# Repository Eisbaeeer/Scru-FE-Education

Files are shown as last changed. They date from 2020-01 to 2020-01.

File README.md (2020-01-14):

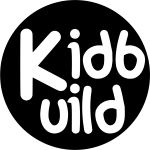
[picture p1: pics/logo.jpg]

# Scru-FE-Education
ESP8266 controlled Scru-FE with routed parts   
Inspirations from : https://www.thingiverse.com/thing:780050

## Beschreibung
Dieses Projekt soll Jugendlichen ab 12 Jahren die Programmierung von Microcontrollern näher bringen. Das Projekt ist dafür 
ausgelegt, z.B. Aktionen als Ferienprogramm anzubieten. Die zeitliche Planung sollte zwei Tage beinhalten. Am ersten Tag wird 
der Roboter aus den gefrästen Teilen zusammengebaut, am zweiten Tag wird er dann programmiert. Weitere Informationen zu dem 
Projekt findet man unter http://www.kidbuild.de
 
## Verzeichnisstruktur
- pics = Bilder
- source = Arduino Sketch
- docs = Anleitung für die Montage des Roboters
- dxf = Fräsdaten für CNC Bearbeitung (4mm Pappel Sperrholz)

## Projektbilder
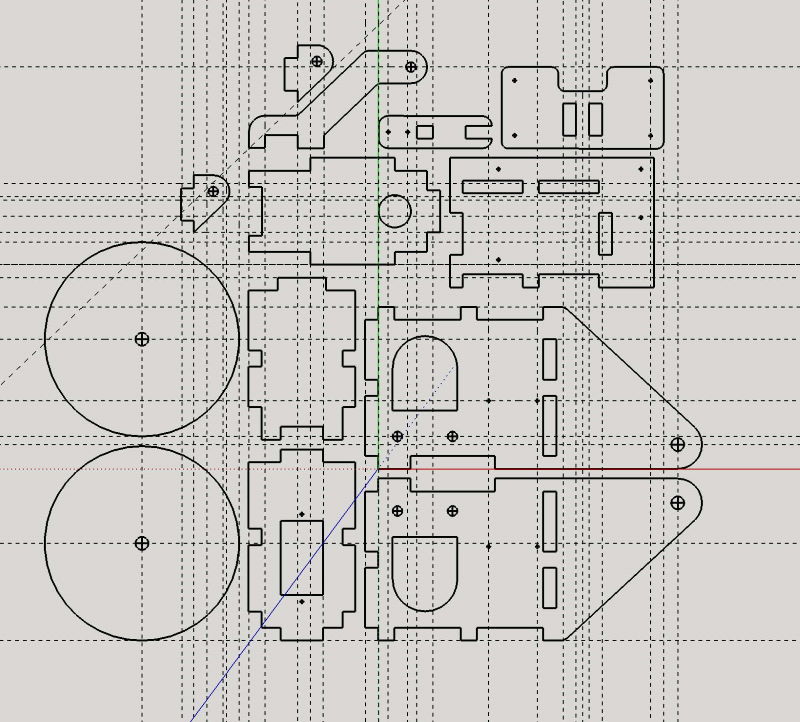
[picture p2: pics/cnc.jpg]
   
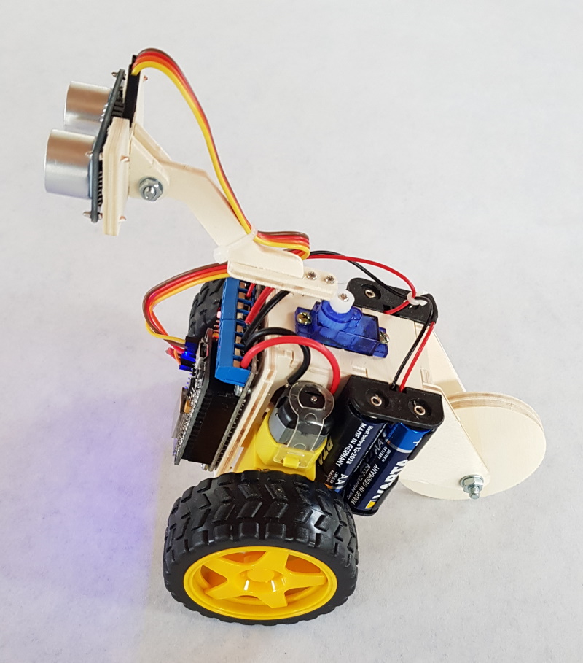
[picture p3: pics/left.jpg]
   
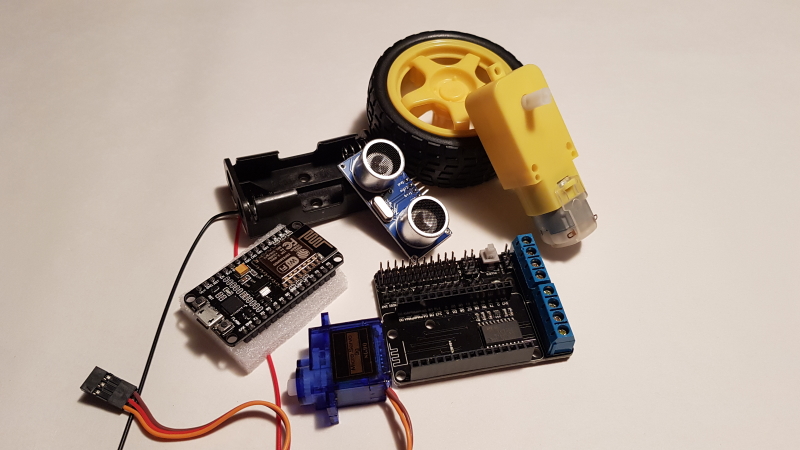
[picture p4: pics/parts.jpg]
   
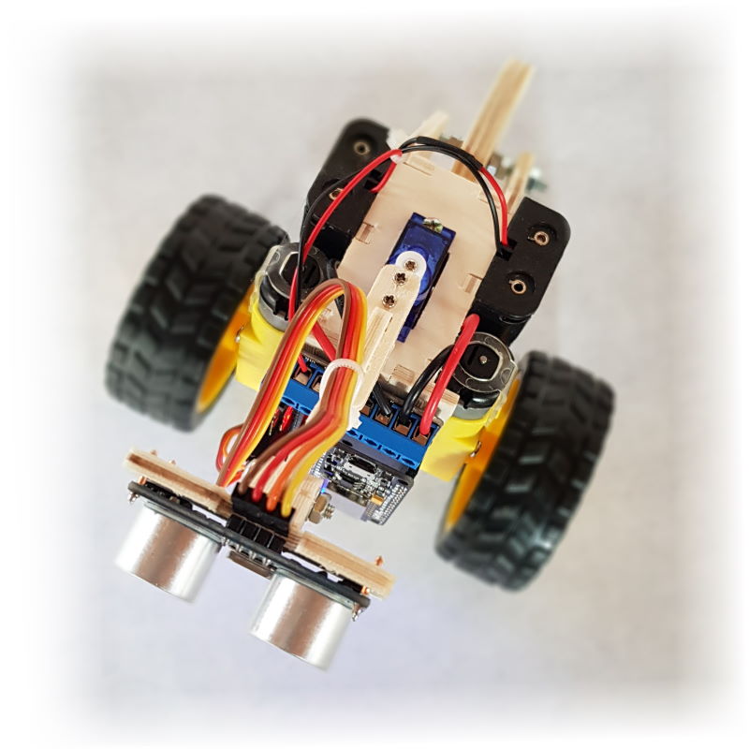
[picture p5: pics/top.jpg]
   

## Changelog

### 1.0
- (Eisbaeeer)
Initial Version

## License
The MIT License (MIT)
Copyright (c) 2019 Eisbaeeer <eisbaeeer@gmail.com>

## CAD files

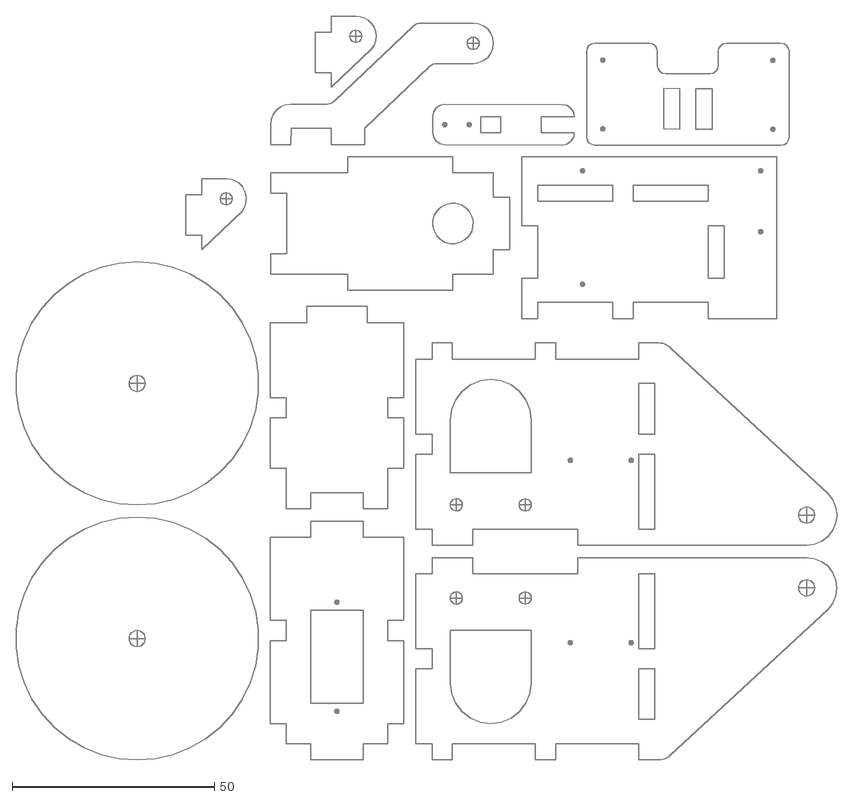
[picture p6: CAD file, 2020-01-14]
dxf/Korpus.dxf
202.8 x 183.7

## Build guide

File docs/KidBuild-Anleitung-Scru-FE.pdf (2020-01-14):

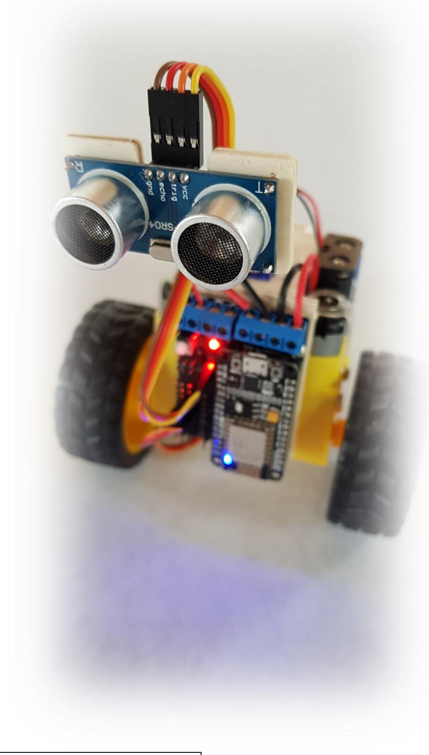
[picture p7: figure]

S e i t e 1 | 26

## SKRU-FE AUFBAU ANLEITUNG

Version | Datum | Bemerkung
1.0 | 13.04.2019 | Initial

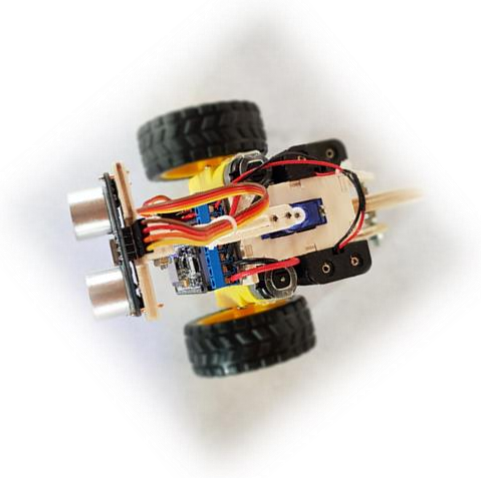
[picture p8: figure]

Roboter lern Projekt www.kidbuild.de

S e i t e 2 | 26

EINLEITUNG

Diese Anleitung hilft Dir dabei, Deinen Scru-FE mit der bebilderten Anleitung Stück für Stück zusammen zu bauen.

Die Teile sind CNC gefräst und müssen noch mit einem Taschenmesser oder scharfer Klinge ausgelöst werden.

Du kannst die Holzteile noch mit Acryl Farbe lackieren oder auch einfach so verwenden.

Der Scru-FE ist nur die Basis für Deine eigenen Ideen. Er lässt sich um weitere Funktionen ergänzen.

Zur Basis gehören die Funktionen ferngesteuertes fahren und autonomes fahren.

Du benötigst dazu lediglich ein WLAN fähiges Gerät mit Browser. Das kann ein Handy oder Tablet sein.

Für das autonome fahren benötigst du kein weiteres Gerät, Dein Scru-FE reicht aus.

Für die Programmierung verwendest du das kostenlose Programm Arduino-IDE. Die Software ist Open-Source und für Windows, Mac und Linux verfügbar.

Dein Scru-FE hat noch freie Schnittstellen, mit denen du Deine eigene Ideen wie Scheinwerfer, Blinklicht, Kamera und viele andere Dinge realisieren kannst.

Weitere Ideen und Anleitungen findest du unter

www.kidbuild.de

Jetzt kann es losgehen! Viel Spaß mit Deinem

SCRU-FE

S e i t e 3 | 26

BAUTEILE
Als erstes löst ihr die gefrästen Teile heraus. Dazu mit einem Taschenmesser oder einer Klinge die Stege vorsichtig von beiden Seiten trennen.

Tipp: Mit einem Schleifpapier die Teile nacharbeiten.

VERLEIMEN DER TEILE

## - Teil G (Frontplatte)

## - Teil I (Seitenteil rechts)

Als erste Teile benötigt ihr die Front (Teil G) und das rechte Seitenteil (Teil I).

Schaut Euch die Zeichnung rechts nochmals genau an und prüft, ob ihr die richtigen Teile vor Euch liegen habt.

Gebt nun auf den Rand zwischen den beiden Teilen ein wenig Holzleim oder Bastelkleber und steckt sie zusammen.

Achtet dabei auf die Frontplatte. Die flache Kante muss nach unten zeigen. Das zweite Bild zeigt, wie die Teile zusammengehören.

## - Teil H

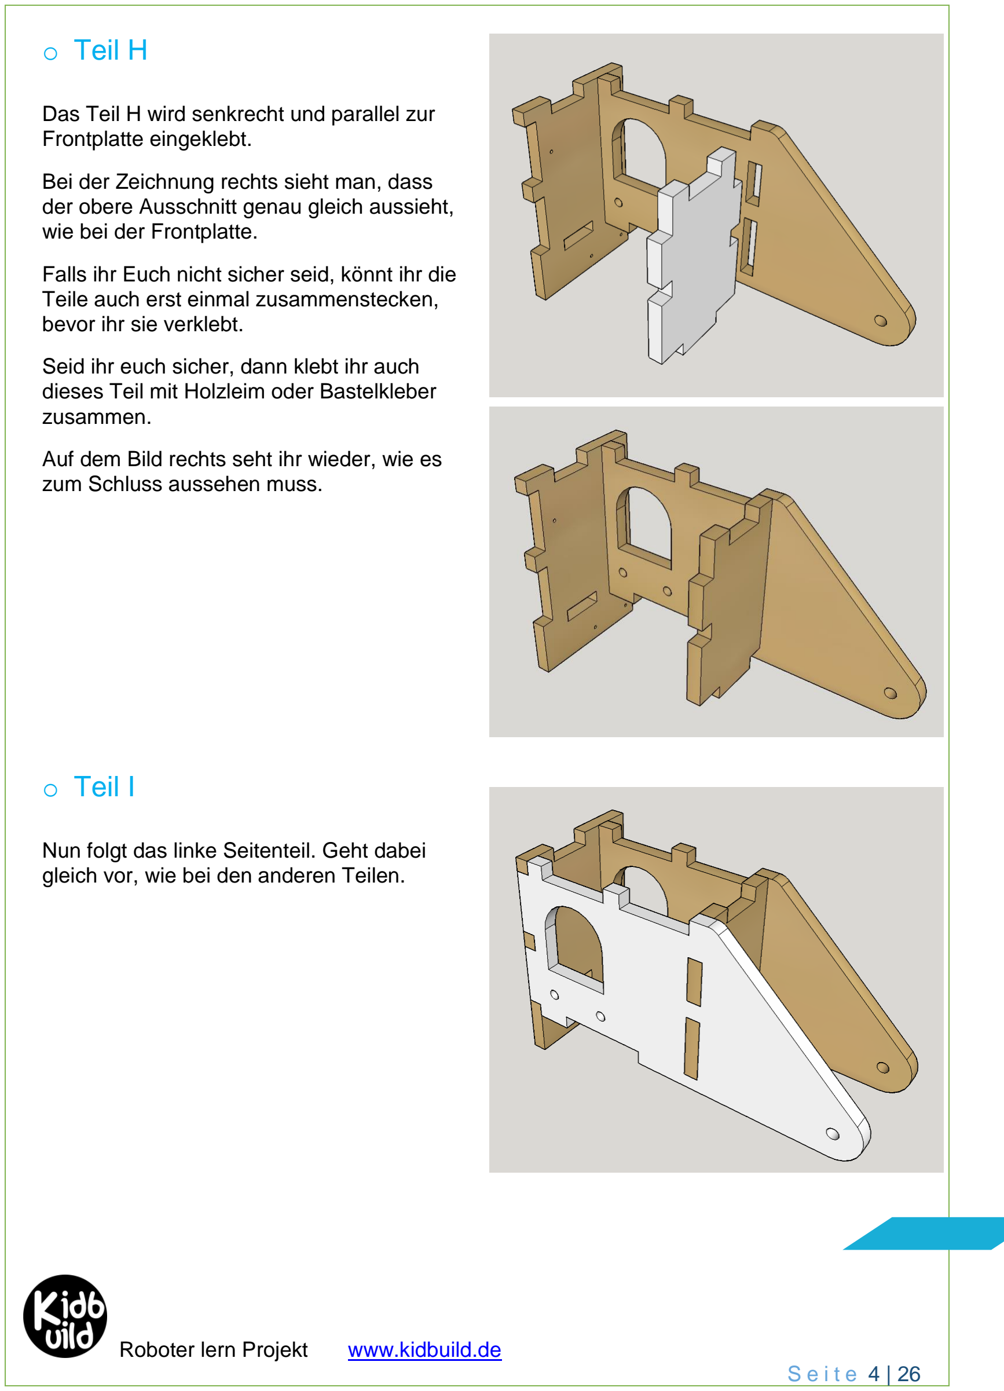
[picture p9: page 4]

S e i t e 4 | 26

Das Teil H wird senkrecht und parallel zur Frontplatte eingeklebt.

Bei der Zeichnung rechts sieht man, dass der obere Ausschnitt genau gleich aussieht, wie bei der Frontplatte.

Falls ihr Euch nicht sicher seid, könnt ihr die Teile auch erst einmal zusammenstecken, bevor ihr sie verklebt.

Seid ihr euch sicher, dann klebt ihr auch dieses Teil mit Holzleim oder Bastelkleber zusammen.

Auf dem Bild rechts seht ihr wieder, wie es zum Schluss aussehen muss.

## - Teil I

Nun folgt das linke Seitenteil. Geht dabei gleich vor, wie bei den anderen Teilen.

## - Teil J

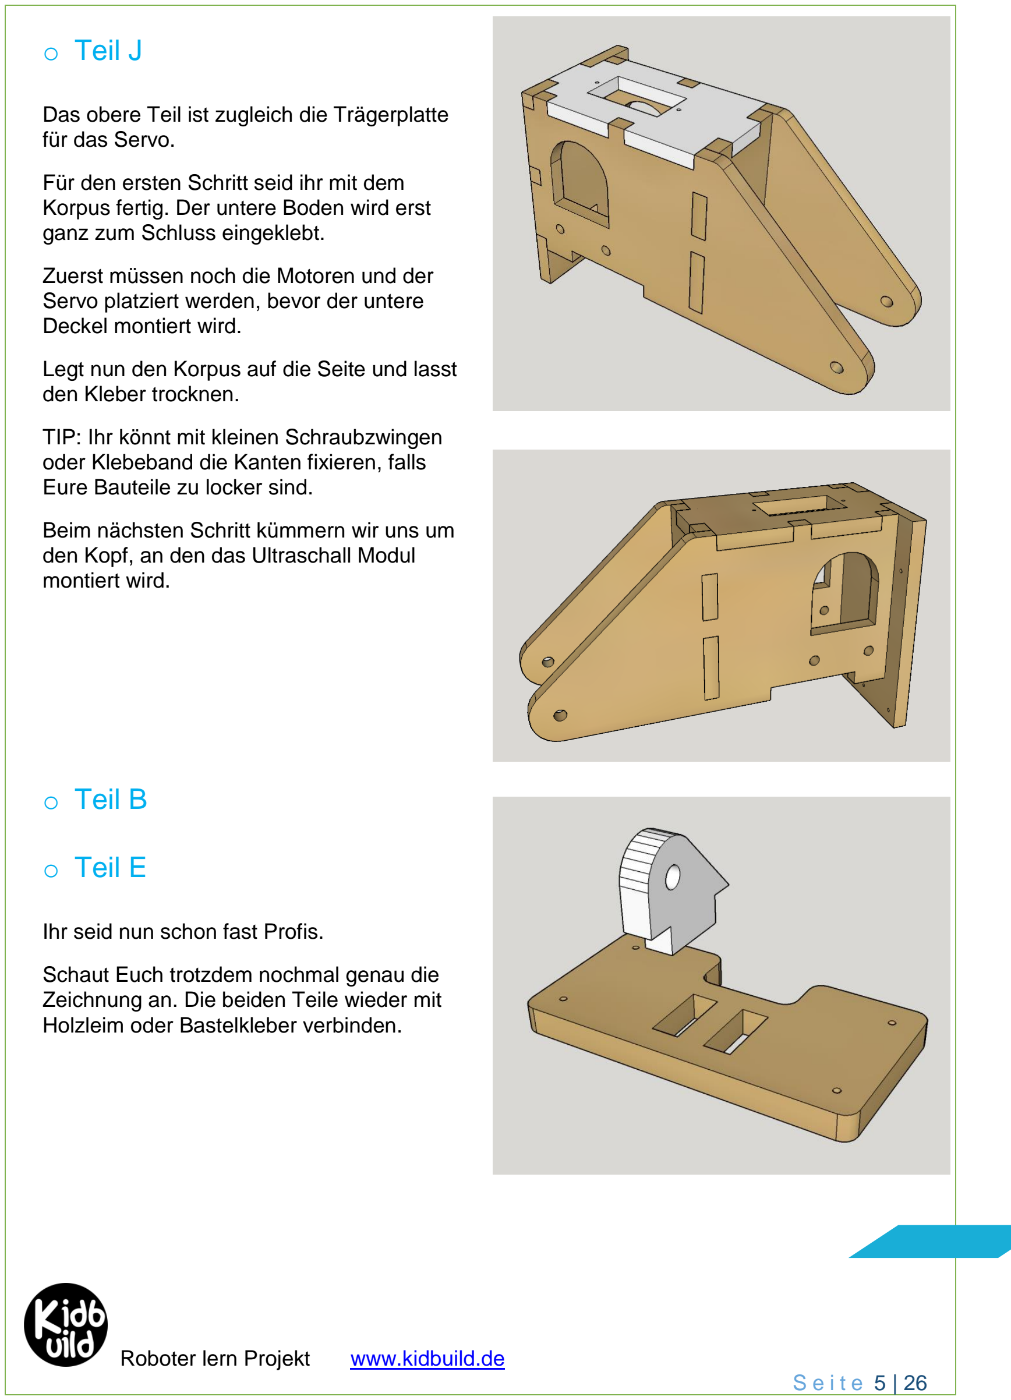
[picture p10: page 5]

S e i t e 5 | 26

Das obere Teil ist zugleich die Trägerplatte für das Servo.

Für den ersten Schritt seid ihr mit dem Korpus fertig. Der untere Boden wird erst ganz zum Schluss eingeklebt.

Zuerst müssen noch die Motoren und der Servo platziert werden, bevor der untere Deckel montiert wird.

Legt nun den Korpus auf die Seite und lasst den Kleber trocknen.

TIP: Ihr könnt mit kleinen Schraubzwingen oder Klebeband die Kanten fixieren, falls Eure Bauteile zu locker sind.

Beim nächsten Schritt kümmern wir uns um den Kopf, an den das Ultraschall Modul montiert wird.

## - Teil B

## - Teil E

Ihr seid nun schon fast Profis.

Schaut Euch trotzdem nochmal genau die Zeichnung an. Die beiden Teile wieder mit Holzleim oder Bastelkleber verbinden.

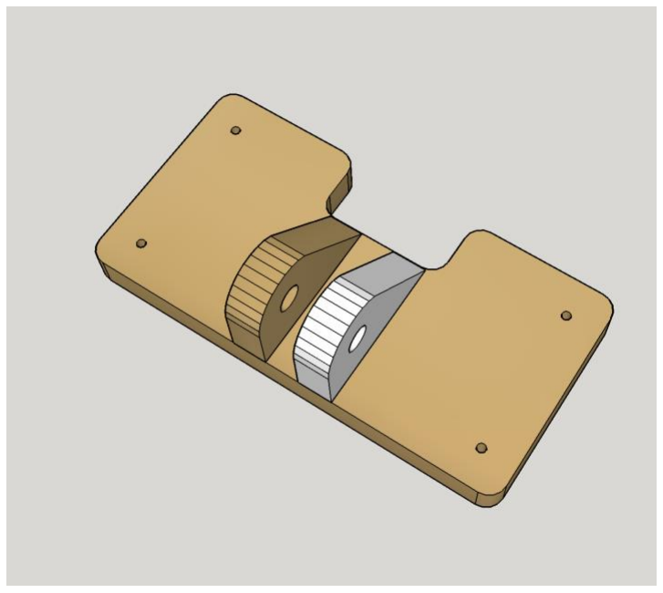
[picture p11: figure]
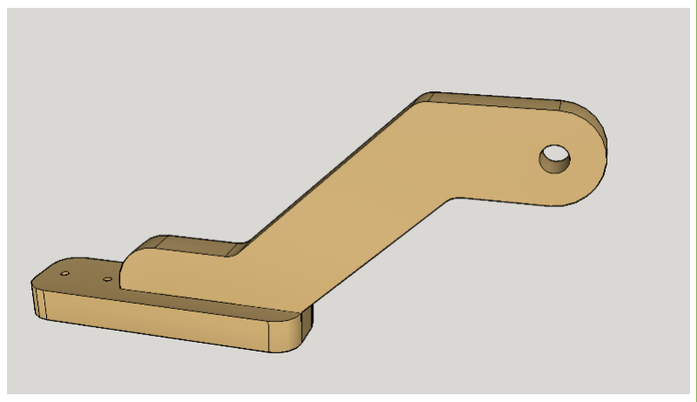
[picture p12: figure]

S e i t e 6 | 26

## - Teil B

Das zweite Teil B genau parallel zum ersten ankleben. Durch die Bohrung kommt später eine Schraube, mit der das Ultraschall Modul geneigt werden kann.

Ihr seht, dass die Bohrung für die Schraube weiter in Richtung unterer Rand angebracht ist.

Legt nach dem Verkleben auch dieses Teil auf die Seite zum Trocknen.

## - Teil C

## - Teil D

Nun zum letzten Teil des Kopfes.

Dieser Teil hält später unser Ultraschall Modul und verbindet es mit dem Servo.

Könnt ihr schon erkennen, wie die Teile zusammengehören?

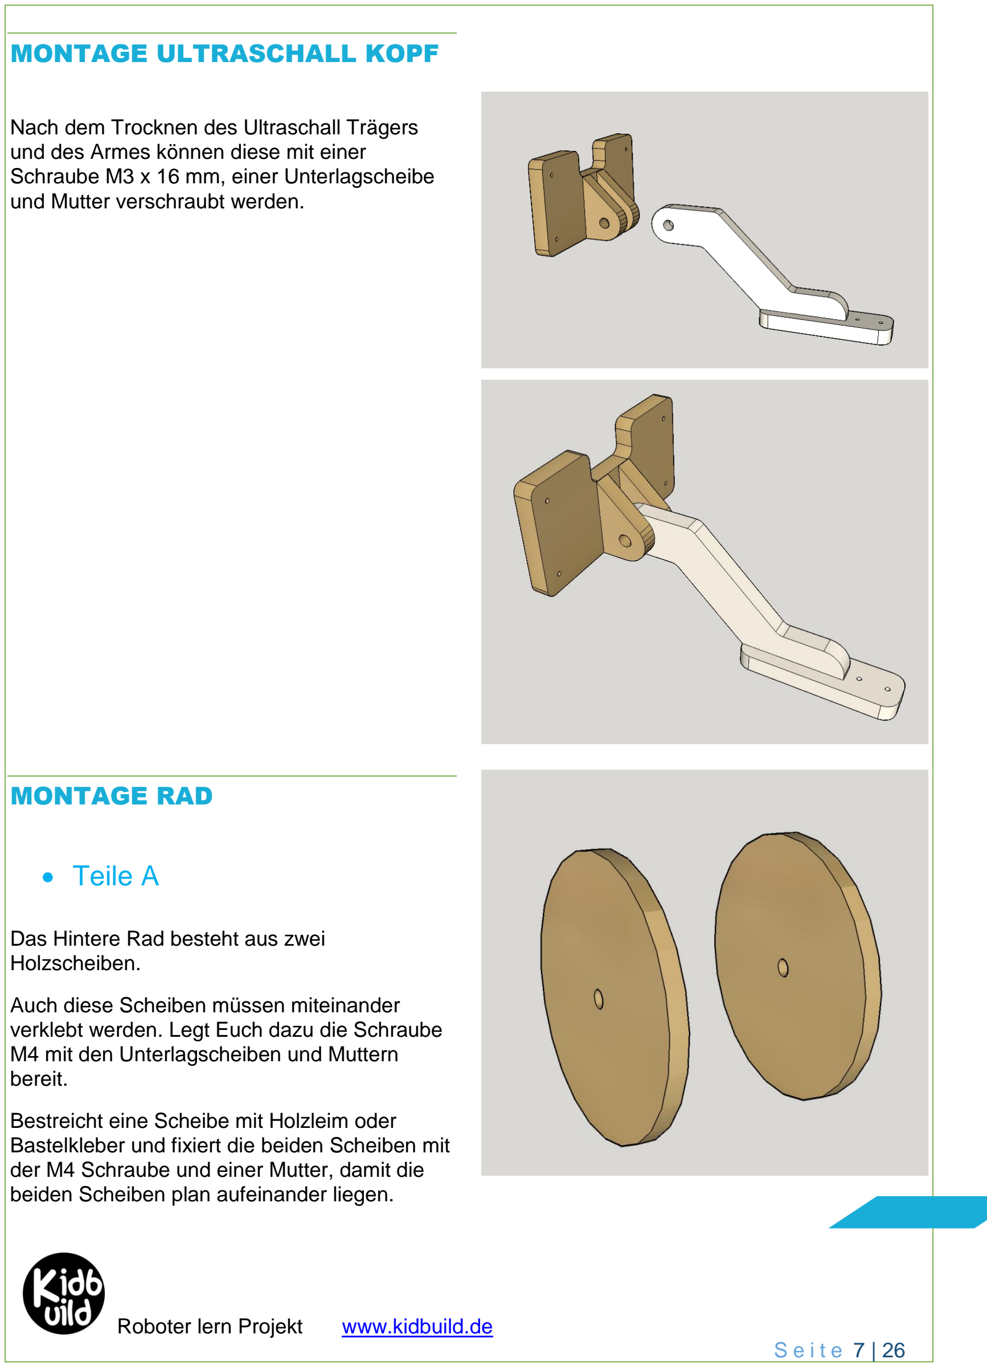
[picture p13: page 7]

S e i t e 7 | 26

MONTAGE ULTRASCHALL KOPF

Nach dem Trocknen des Ultraschall Trägers und des Armes können diese mit einer Schraube M3 x 16 mm, einer Unterlagscheibe und Mutter verschraubt werden.

MONTAGE RAD

## - Teile A

Das Hintere Rad besteht aus zwei Holzscheiben.

Auch diese Scheiben müssen miteinander verklebt werden. Legt Euch dazu die Schraube M4 mit den Unterlagscheiben und Muttern bereit.

Bestreicht eine Scheibe mit Holzleim oder Bastelkleber und fixiert die beiden Scheiben mit der M4 Schraube und einer Mutter, damit die beiden Scheiben plan aufeinander liegen.

S e i t e 8 | 26

Legt nun das Hinterrad auf die Seite zum Trocknen.

Nun habt ihr erstmal alle nötigen Teile miteinander verklebt. Seht nun nach, ob Euer Korpus bereits getrocknet ist.

Mit ihm geht es jetzt weiter.

BAUTEIL LISTE
Hier findet ihr eine Auflistung der restlichen Bauteile
Anzahl | Bezeichnung
1 | Schraube M4 x 40mm
3 | Mutter M4
4 | Schraube M3 x 30mm
1 | Schraube M3 x 16mm
5 | Mutter M3
10 | Holzschraube 2mm x 10mm
1 | Micro Servo SG90
1 | Ultraschall Modul HC-SR04
1 | Motor Shield Development Board
1 | NodeMcu Lua ESP8266 passend zum Motor Shield (gibt es auch als Kit mit Shield)
1 | Piezo Signalgeber 5V (optional)
2 | AA Batteriebox mit Kabel
1 | 20cm Litze rot/schwarz
1 | 10cm 1,5 mm² Kupfer Draht
6 | Breadboard Litze Buchse/Buchse 20cm Länge
2 | Getriebemotor mit Rad (COM MOTOR RAD)
1 | Holzleim
1 | Schraubensicherung (alternativ selbstsichernde Muttern oder 2 x Kontermuttern M4)
1 | Schrumpfschlauch ca. 2cm
2 | Kabelbinder
1 | USB micro Kabel
4 | AA Batterien
1 | Jumper Steckbrücke RM 2,45

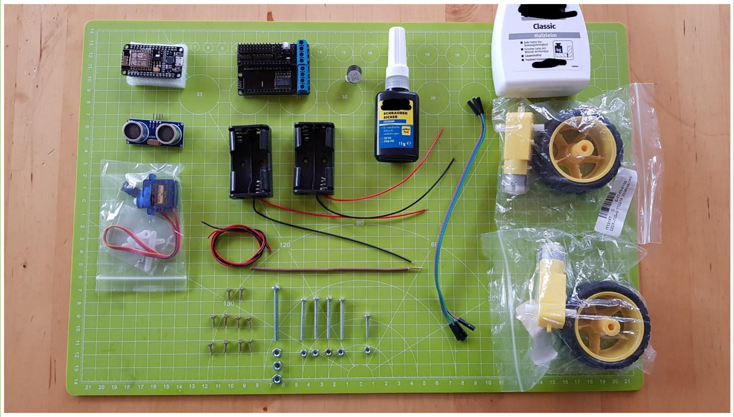
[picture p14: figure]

S e i t e 9 | 26

ÜBERSICHT

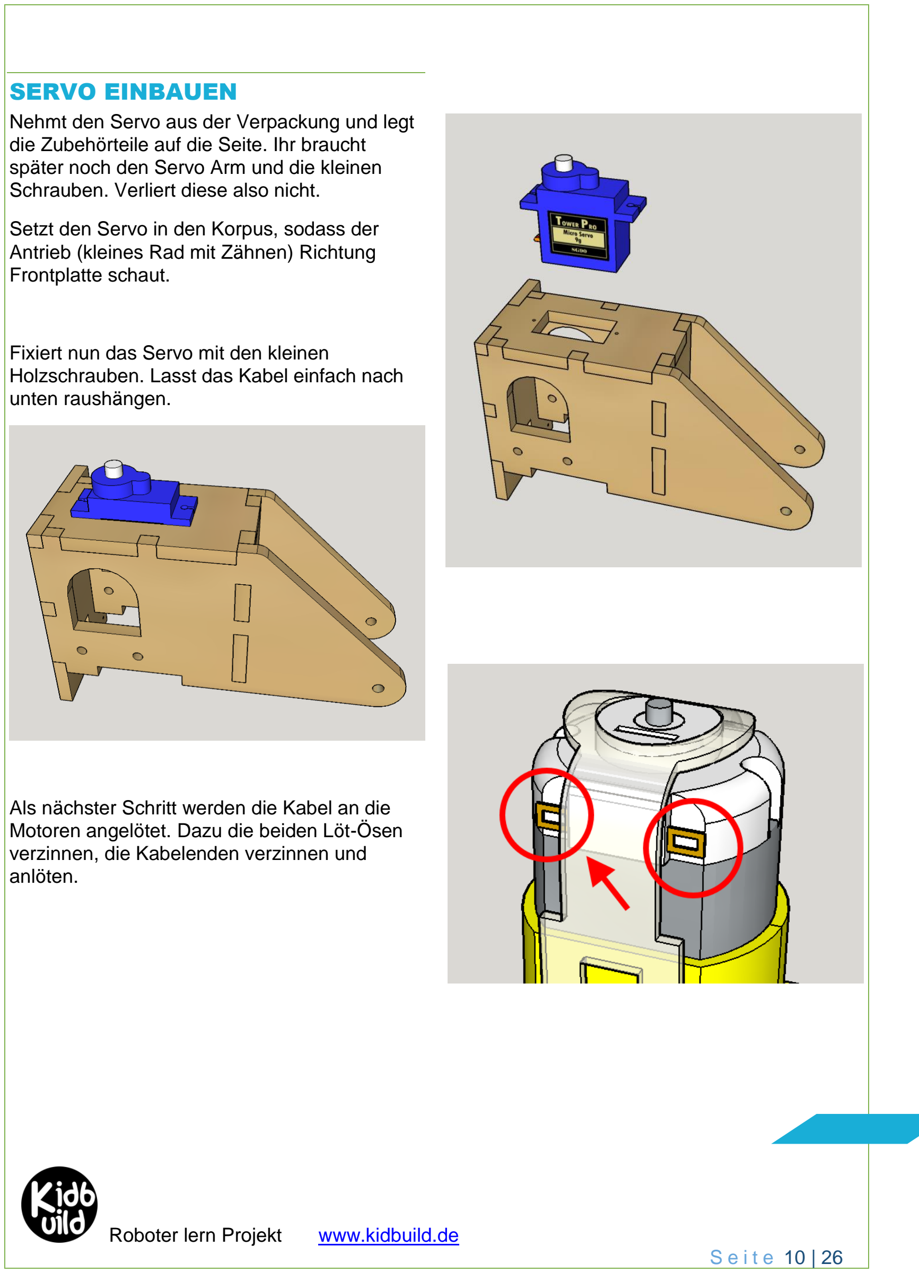
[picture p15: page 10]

S e i t e 10 | 26

SERVO EINBAUEN
Nehmt den Servo aus der Verpackung und legt die Zubehörteile auf die Seite. Ihr braucht später noch den Servo Arm und die kleinen Schrauben. Verliert diese also nicht.

Setzt den Servo in den Korpus, sodass der Antrieb (kleines Rad mit Zähnen) Richtung Frontplatte schaut.

Fixiert nun das Servo mit den kleinen Holzschrauben. Lasst das Kabel einfach nach unten raushängen.

Als nächster Schritt werden die Kabel an die Motoren angelötet. Dazu die beiden Löt-Ösen verzinnen, die Kabelenden verzinnen und anlöten.

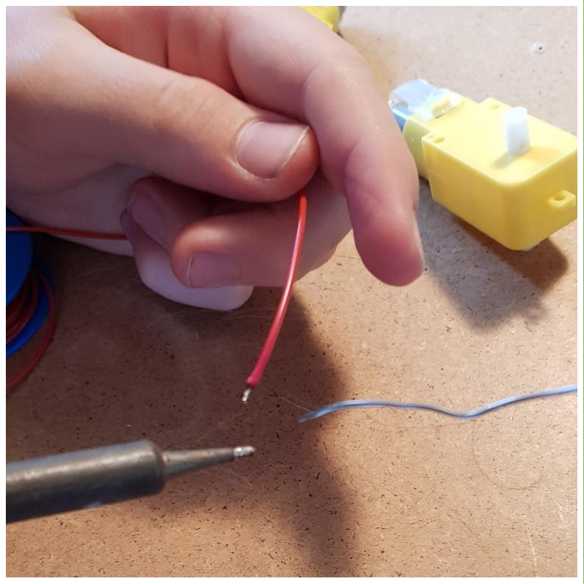
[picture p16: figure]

S e i t e 11 | 26

Beim Verzinnen den Lötkolben kurz an den blanken Draht halten und ein wenig Lötzinn zuführen. Wenn das Lötzinn verschmolzen ist, den Lötkolben sofort vom Draht entfernen.

Jeder Motor bekommt einen schwarzen und einen roten Draht angelötet.

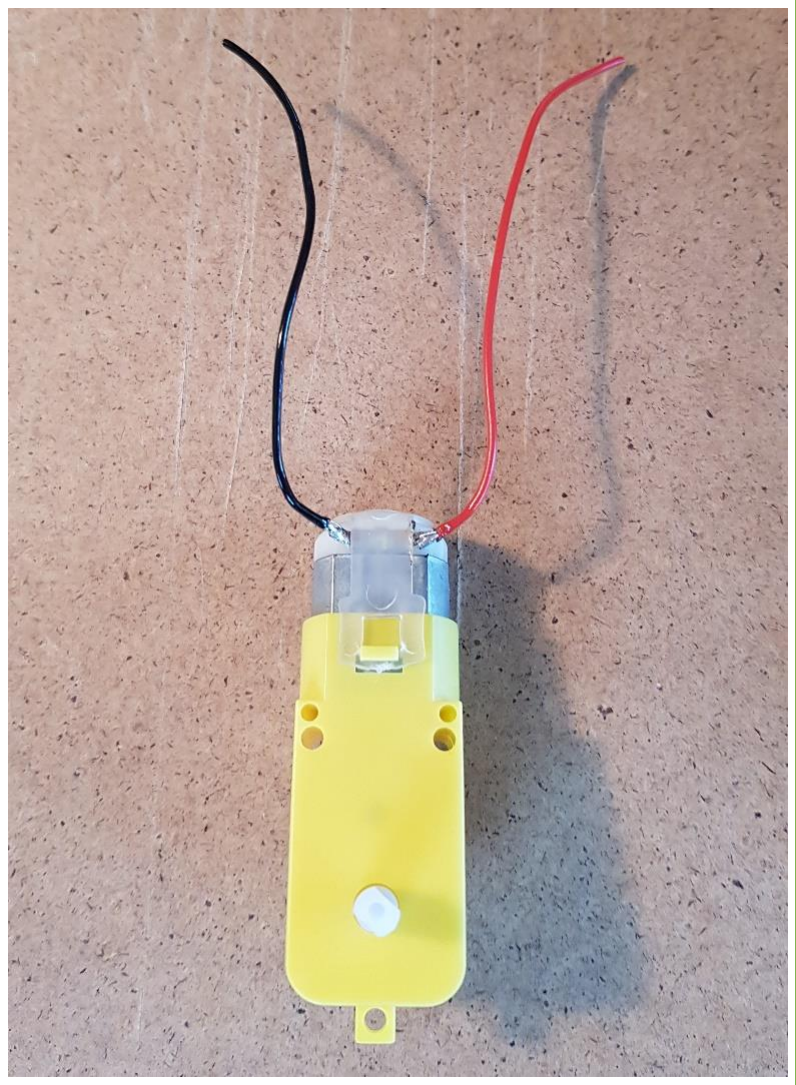
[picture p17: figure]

S e i t e 12 | 26

Die Drähte auf ca. 10cm kürzen. Wenn ihr fertig seid, sollte es so aussehen.

Wiederholt das ganze mit dem zweiten Motor.

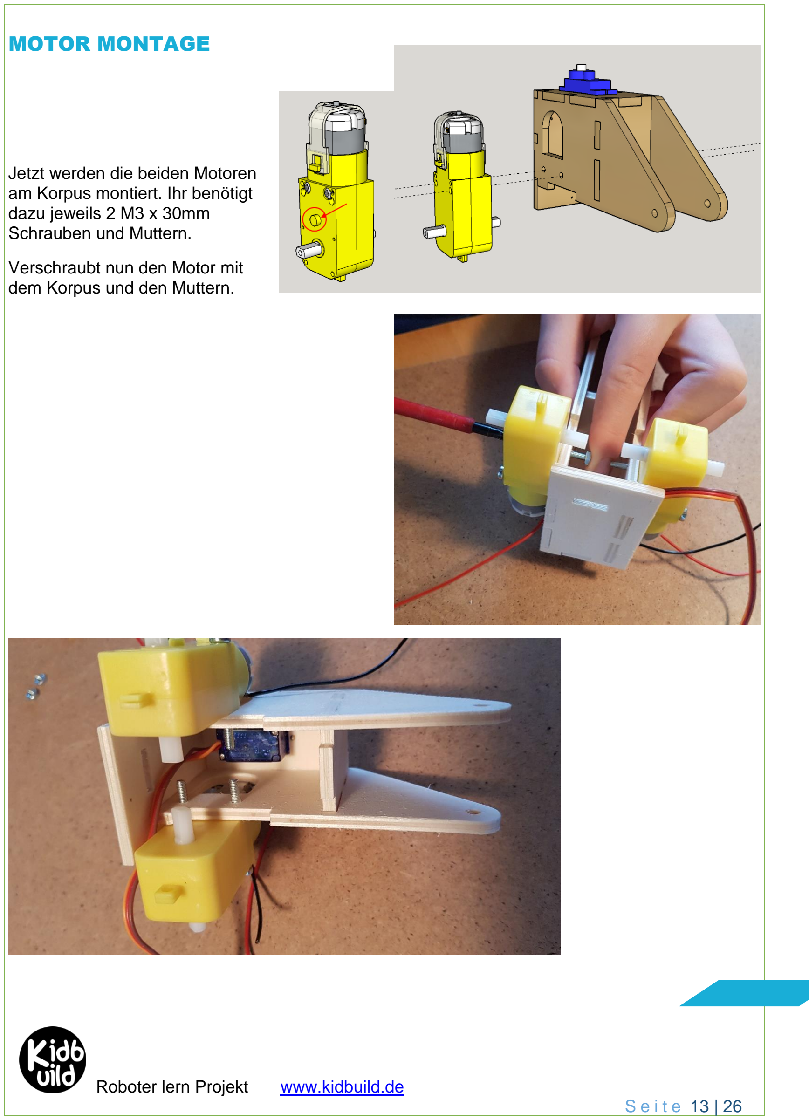
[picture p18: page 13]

S e i t e 13 | 26

MOTOR MONTAGE

Jetzt werden die beiden Motoren am Korpus montiert. Ihr benötigt dazu jeweils 2 M3 x 30mm
Schrauben und Muttern.

Verschraubt nun den Motor mit dem Korpus und den Muttern.

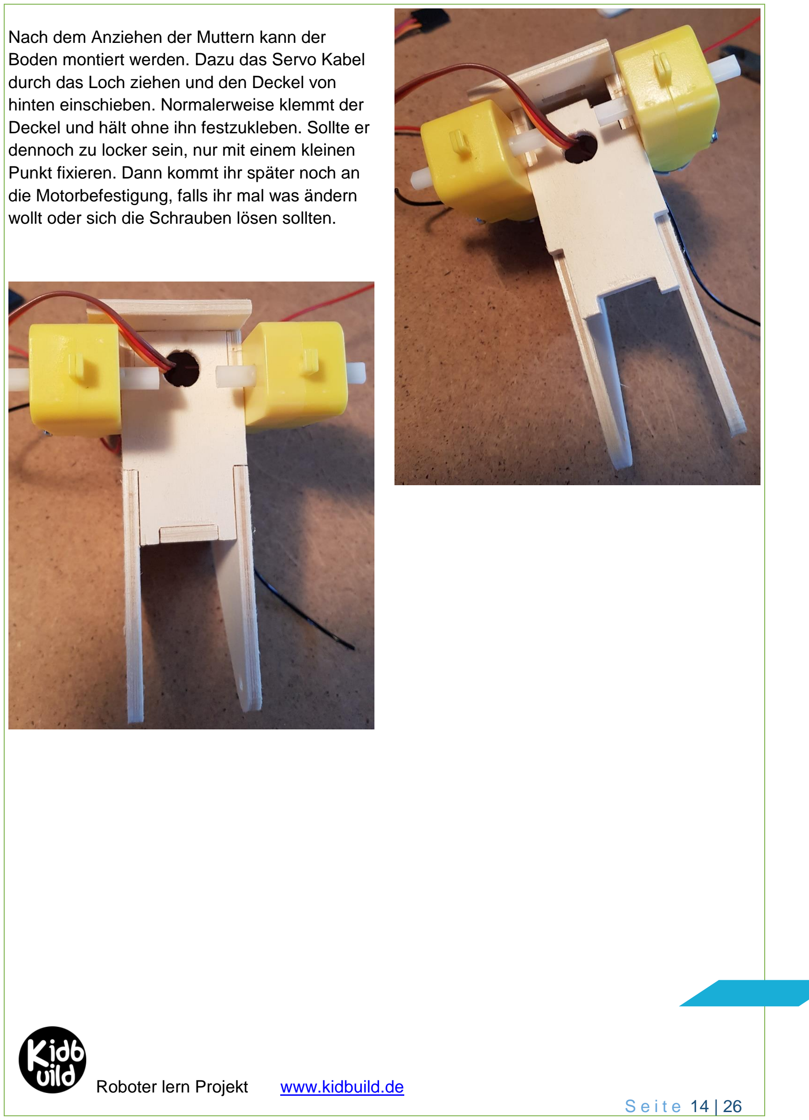
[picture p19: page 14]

S e i t e 14 | 26

Nach dem Anziehen der Muttern kann der Boden montiert werden. Dazu das Servo Kabel durch das Loch ziehen und den Deckel von hinten einschieben. Normalerweise klemmt der Deckel und hält ohne ihn festzukleben. Sollte er dennoch zu locker sein, nur mit einem kleinen Punkt fixieren. Dann kommt ihr später noch an die Motorbefestigung, falls ihr mal was ändern wollt oder sich die Schrauben lösen sollten.

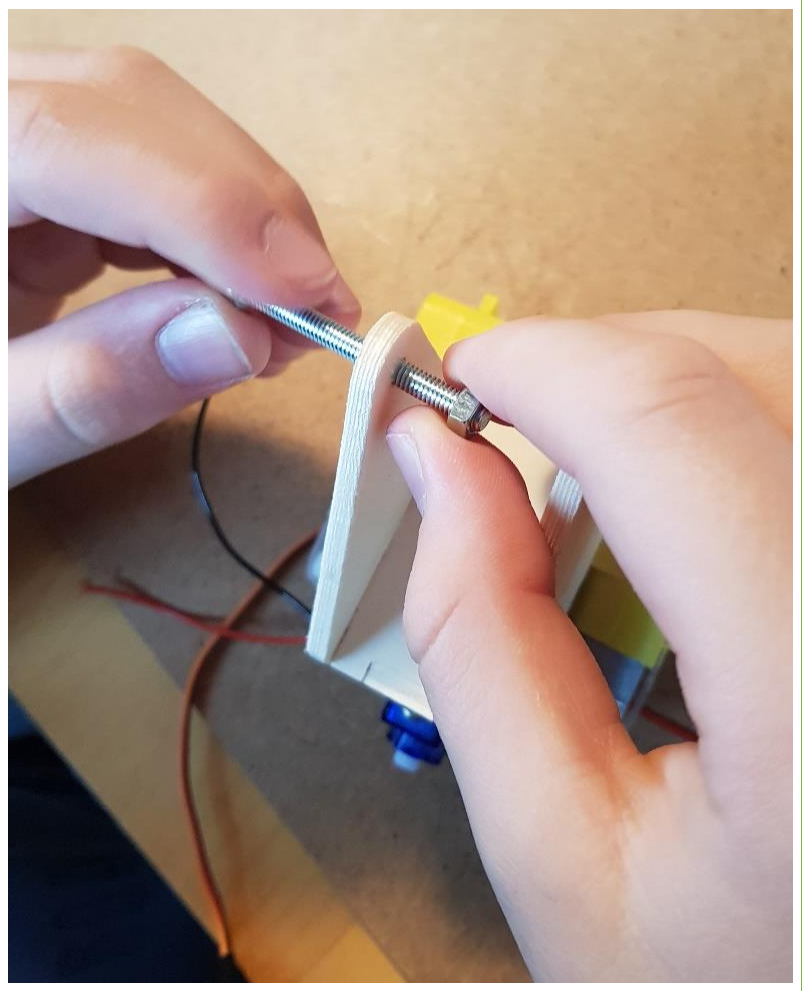
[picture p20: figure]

S e i t e 15 | 26

MONTAGE HINTERES RAD
Für das hintere Rad braucht ihr die M4 x 30mm Schraube. Eventuell habt ihr sie für das Zusammenleimen noch am Rad montiert.

Schraubt diese los und schiebt sie durch das hintere Loch und befestigt die erste Mutter.

Jetzt wird das Rad auf die Schraube gesteckt und wieder eine Mutter. Dreht nun die Schraube ganz ein.

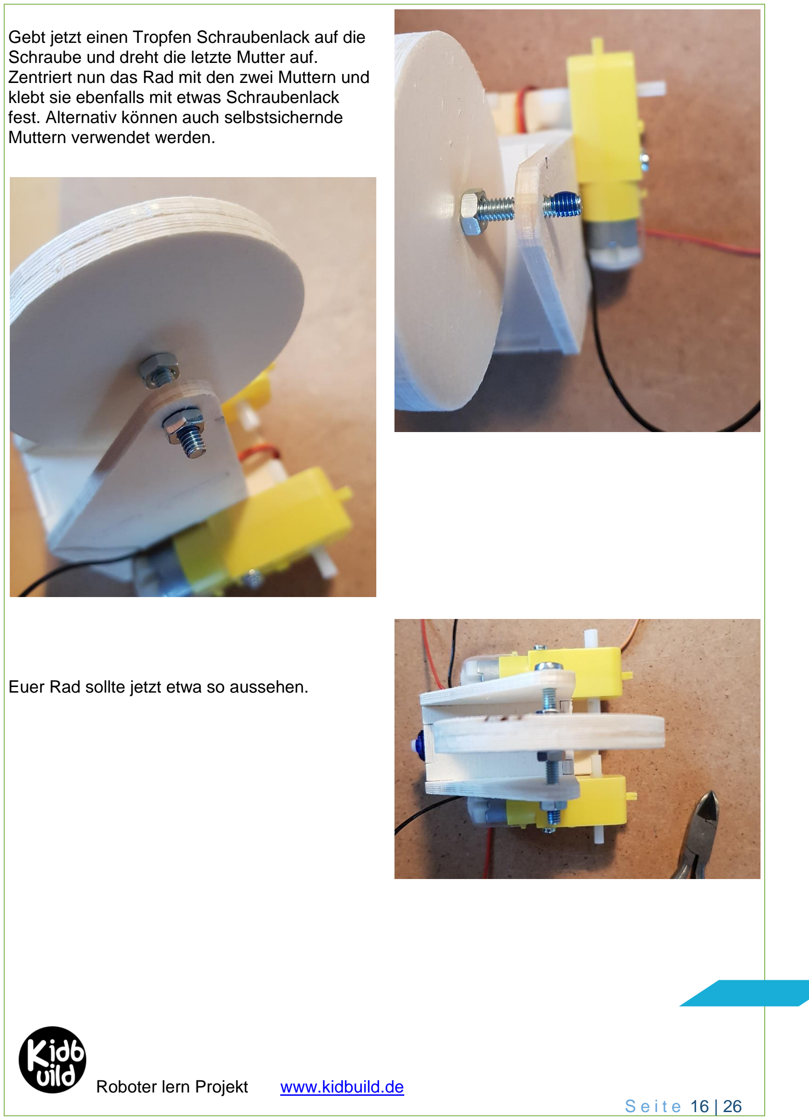
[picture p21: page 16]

S e i t e 16 | 26

Gebt jetzt einen Tropfen Schraubenlack auf die Schraube und dreht die letzte Mutter auf. Zentriert nun das Rad mit den zwei Muttern und klebt sie ebenfalls mit etwas Schraubenlack fest. Alternativ können auch selbstsichernde Muttern verwendet werden.

Euer Rad sollte jetzt etwa so aussehen.

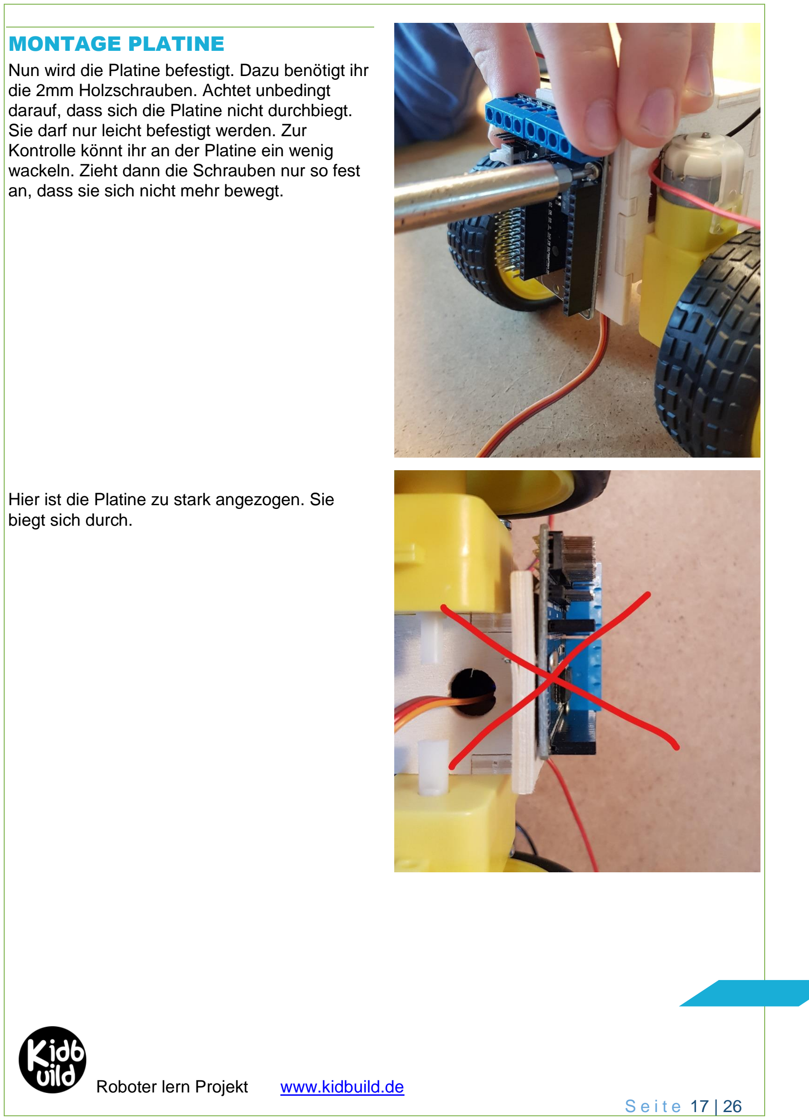
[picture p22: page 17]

S e i t e 17 | 26

MONTAGE PLATINE
Nun wird die Platine befestigt. Dazu benötigt ihr die 2mm Holzschrauben. Achtet unbedingt darauf, dass sich die Platine nicht durchbiegt. Sie darf nur leicht befestigt werden. Zur Kontrolle könnt ihr an der Platine ein wenig wackeln. Zieht dann die Schrauben nur so fest an, dass sie sich nicht mehr bewegt.

Hier ist die Platine zu stark angezogen. Sie biegt sich durch.

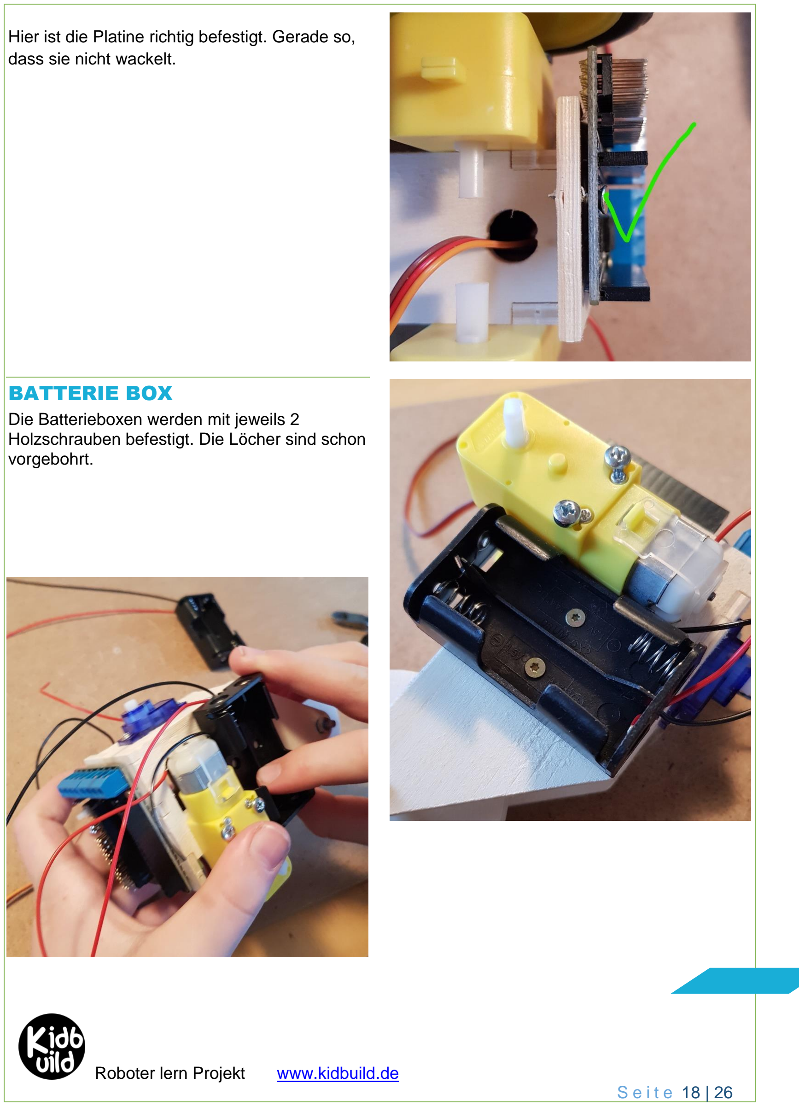
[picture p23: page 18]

S e i t e 18 | 26

Hier ist die Platine richtig befestigt. Gerade so, dass sie nicht wackelt.

BATTERIE BOX
Die Batterieboxen werden mit jeweils 2 Holzschrauben befestigt. Die Löcher sind schon vorgebohrt.

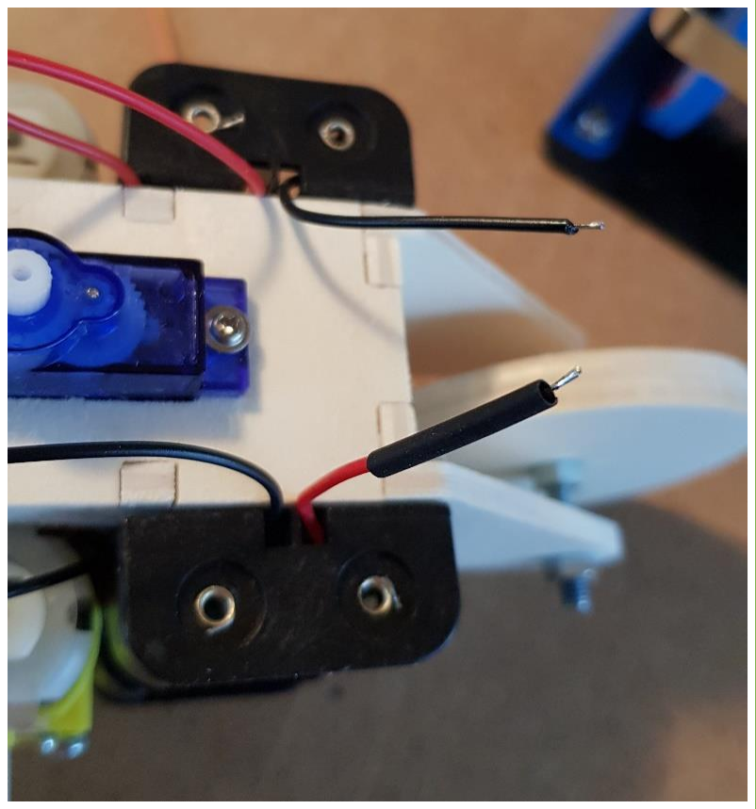
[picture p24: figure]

S e i t e 19 | 26

VERKABELN
Nachdem die Batteriebox befestigt ist, müssen wir nochmals ein wenig löten. Wir benötigen für den Betrieb des Scru-FE etwa 6V. Damit wir die 6V erreichen, müssen wir alle vier Batterien in Reihe schalten. Nun sind zwei Batterien in der Batteriebox schon in Reihe geschaltet und ergeben etwa 3V. Das bedeutet, dass wir die beiden Batterieboxen nochmals in Reihe schalten müssen, damit wir auf die 6V Spannung kommen.

Hier mal die Rechnung:

Eine Batterie hat bei voller Kapazität 1,5V Spannung.

1,5V + 1,5V + 1,5V + 1,5V = 6V

Kürzt nun einen schwarzen Draht von der rechten und einen roten Draht von der linken Batteriebox auf genau die Länge, sodass ihr sie miteinander verlöten könnt. Schiebt vor dem Verlöten noch ein Stück Schrumpfschlauch über ein Ende des Kabels. Achtet darauf, dass der Schrumpfschlauch nicht zu nah an der Lötstelle ist, denn er schrumpft bei Hitze zusammen.

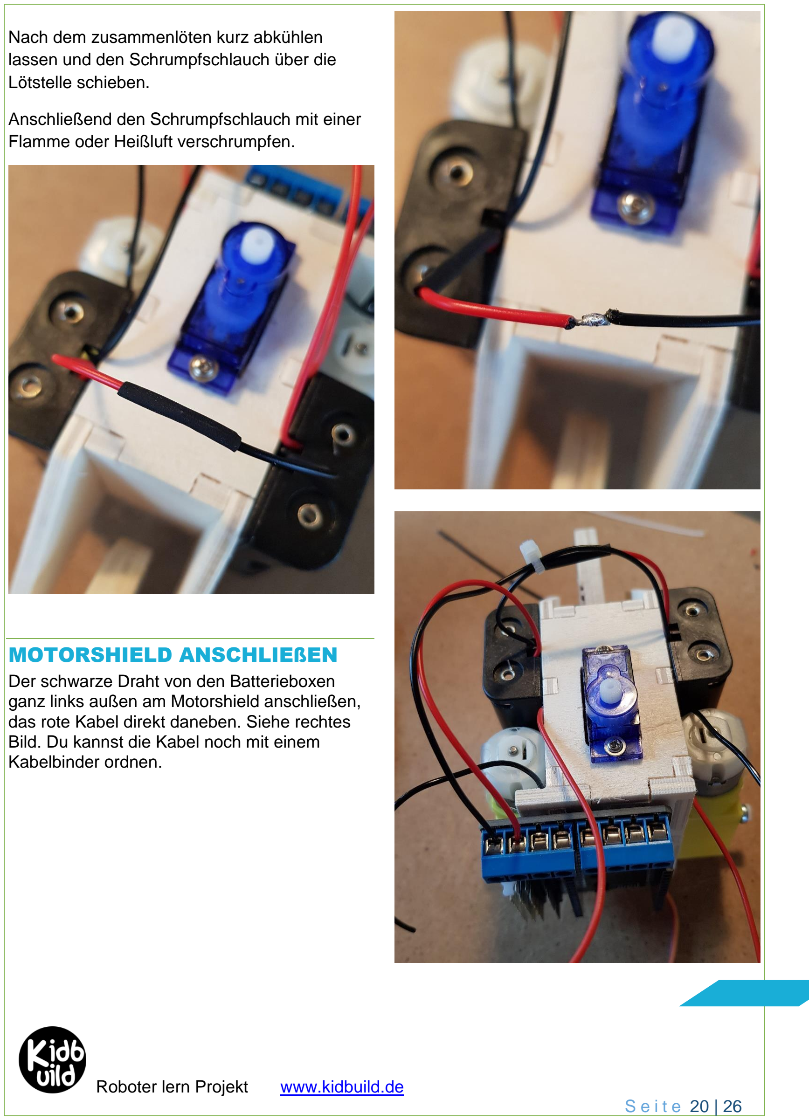
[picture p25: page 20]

S e i t e 20 | 26

Nach dem zusammenlöten kurz abkühlen lassen und den Schrumpfschlauch über die Lötstelle schieben.

Anschließend den Schrumpfschlauch mit einer Flamme oder Heißluft verschrumpfen.

MOTORSHIELD ANSCHLIEßEN
Der schwarze Draht von den Batterieboxen ganz links außen am Motorshield anschließen, das rote Kabel direkt daneben. Siehe rechtes Bild. Du kannst die Kabel noch mit einem Kabelbinder ordnen.

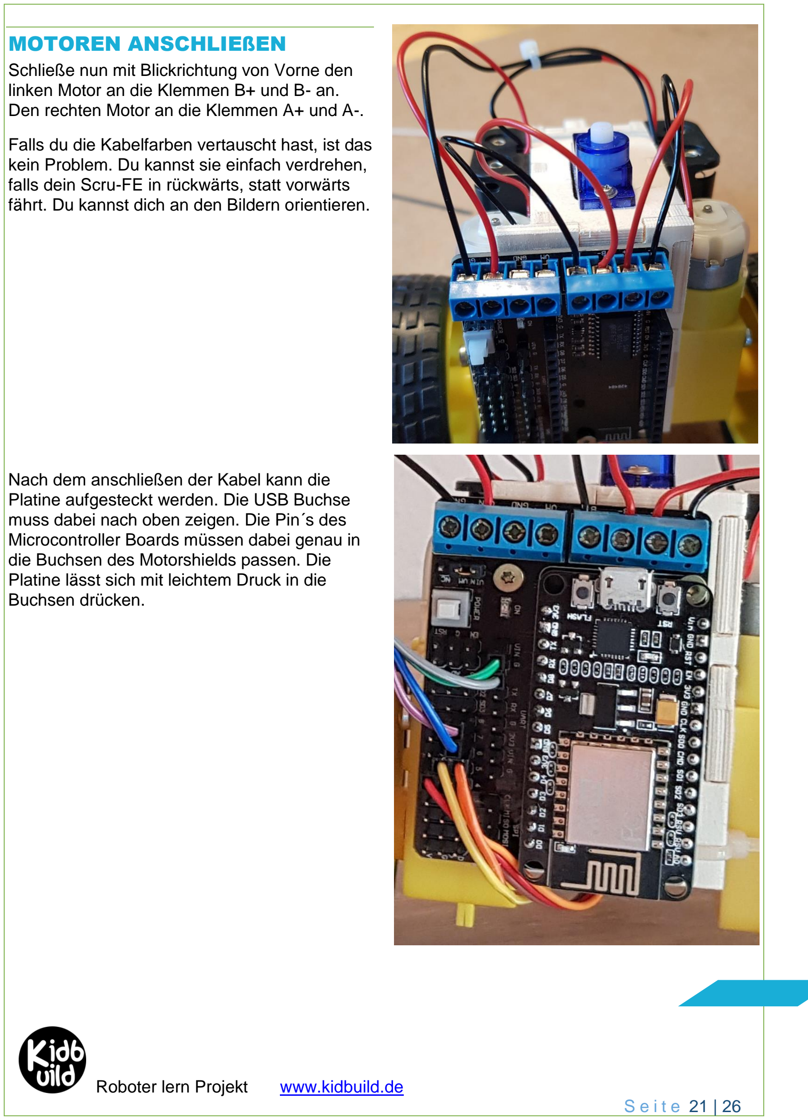
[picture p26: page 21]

S e i t e 21 | 26

MOTOREN ANSCHLIEßEN
Schließe nun mit Blickrichtung von Vorne den linken Motor an die Klemmen B+ und B- an. Den rechten Motor an die Klemmen A+ und A-.

Falls du die Kabelfarben vertauscht hast, ist das kein Problem. Du kannst sie einfach verdrehen, falls dein Scru-FE in rückwärts, statt vorwärts fährt. Du kannst dich an den Bildern orientieren.

Nach dem anschließen der Kabel kann die Platine aufgesteckt werden. Die USB Buchse muss dabei nach oben zeigen. Die Pin´s des Microcontroller Boards müssen dabei genau in die Buchsen des Motorshields passen. Die Platine lässt sich mit leichtem Druck in die Buchsen drücken.

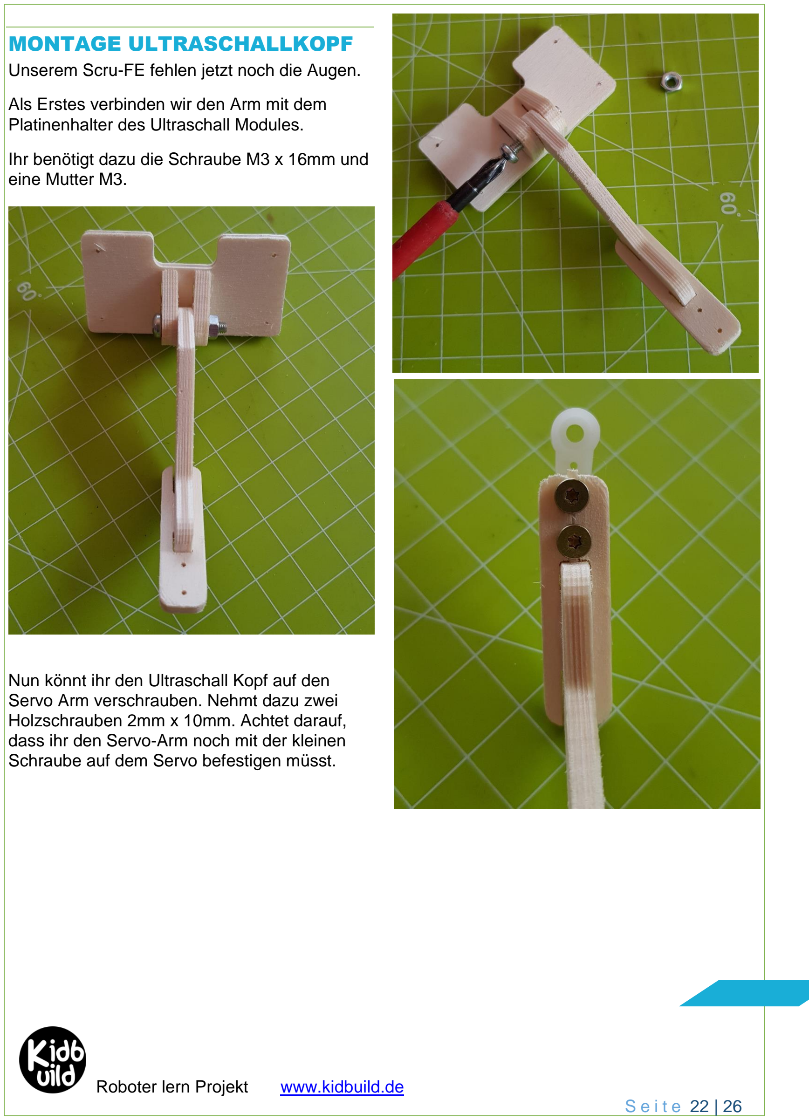
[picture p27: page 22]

S e i t e 22 | 26

MONTAGE ULTRASCHALLKOPF
Unserem Scru-FE fehlen jetzt noch die Augen.

Als Erstes verbinden wir den Arm mit dem Platinenhalter des Ultraschall Modules.

Ihr benötigt dazu die Schraube M3 x 16mm und eine Mutter M3.

Nun könnt ihr den Ultraschall Kopf auf den Servo Arm verschrauben. Nehmt dazu zwei Holzschrauben 2mm x 10mm. Achtet darauf, dass ihr den Servo-Arm noch mit der kleinen Schraube auf dem Servo befestigen müsst.

S e i t e 23 | 26

ULTRASCHALL PLATINE
BEFESTIGEN
Isoliert den Kupferdraht 1,5mm² ab. Biegt den Draht möglichst gerade und steckt diesen in den Platinenhalter. Zwickt ihn bei etwa einem Zentimeter ab.

Das Ganze sollte dann etwa so wie rechts auf dem Bild aussehen. Passt auf Eure Finger auf. Der Draht geht etwas schwer in das Holz. Nehmt eventuell eine Zange zur Hilfe.

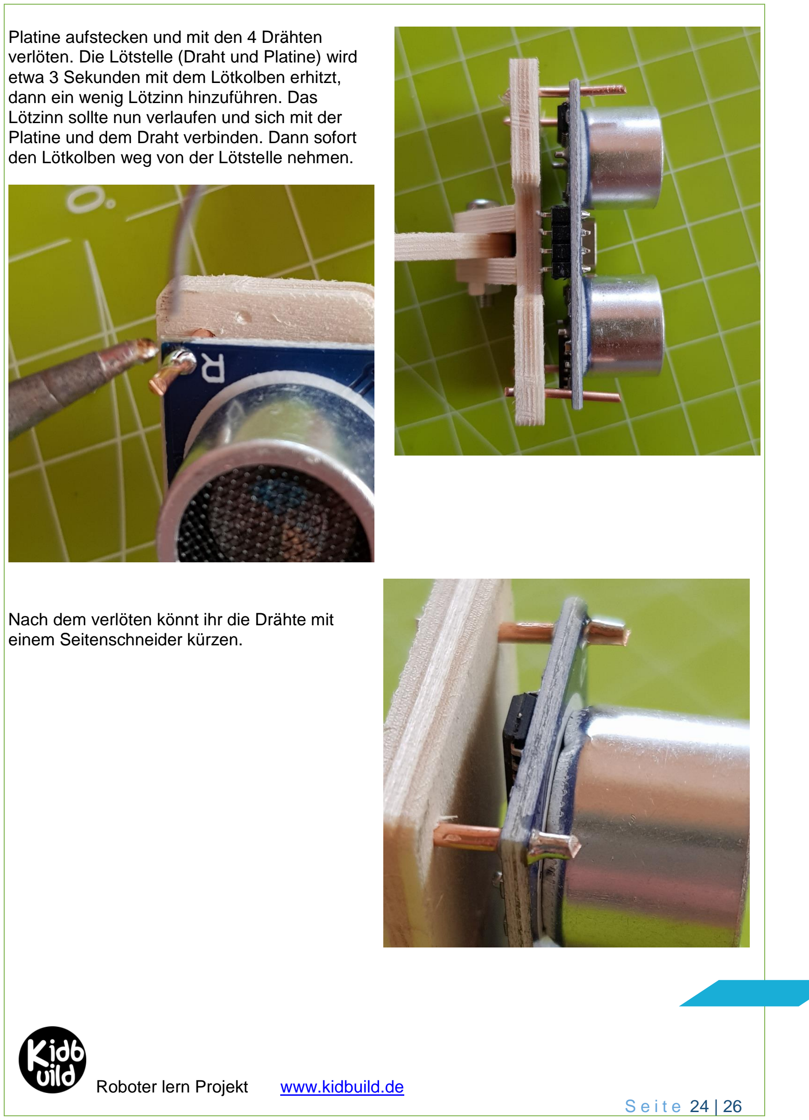
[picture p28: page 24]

S e i t e 24 | 26

Platine aufstecken und mit den 4 Drähten verlöten. Die Lötstelle (Draht und Platine) wird etwa 3 Sekunden mit dem Lötkolben erhitzt, dann ein wenig Lötzinn hinzuführen. Das Lötzinn sollte nun verlaufen und sich mit der Platine und dem Draht verbinden. Dann sofort den Lötkolben weg von der Lötstelle nehmen.

Nach dem verlöten könnt ihr die Drähte mit einem Seitenschneider kürzen.

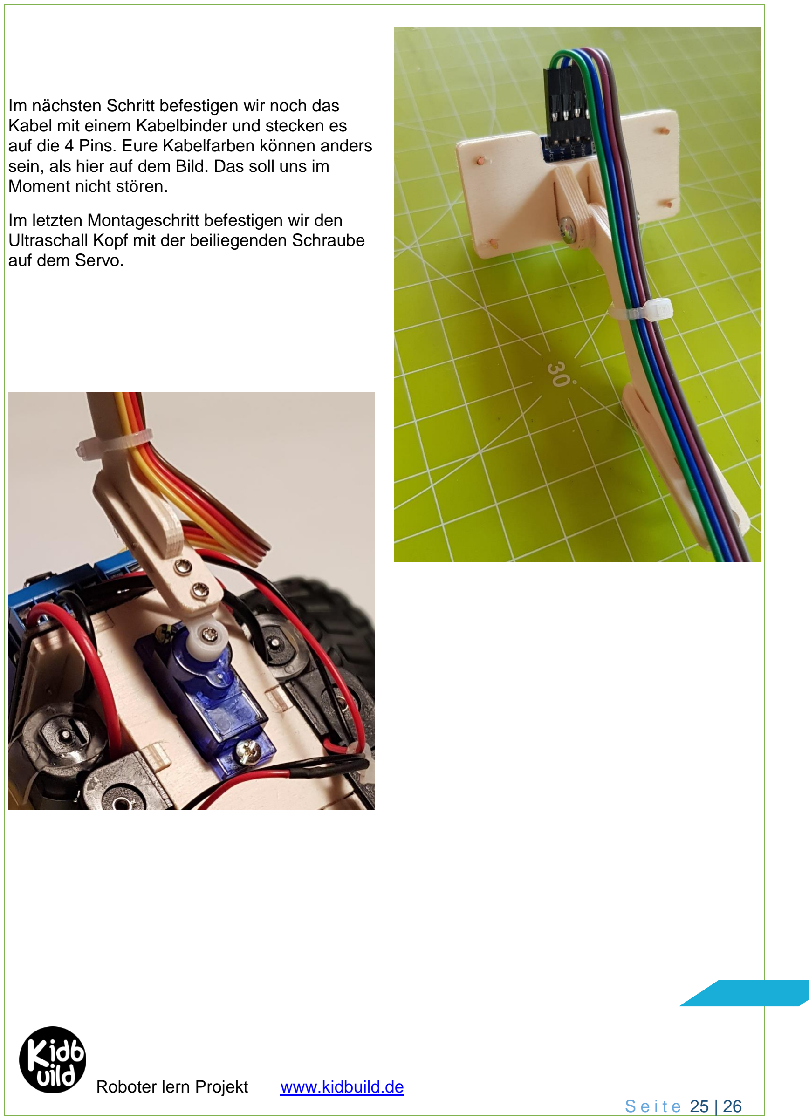
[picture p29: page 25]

S e i t e 25 | 26

Im nächsten Schritt befestigen wir noch das Kabel mit einem Kabelbinder und stecken es auf die 4 Pins. Eure Kabelfarben können anders sein, als hier auf dem Bild. Das soll uns im Moment nicht stören.

Im letzten Montageschritt befestigen wir den Ultraschall Kopf mit der beiliegenden Schraube auf dem Servo.

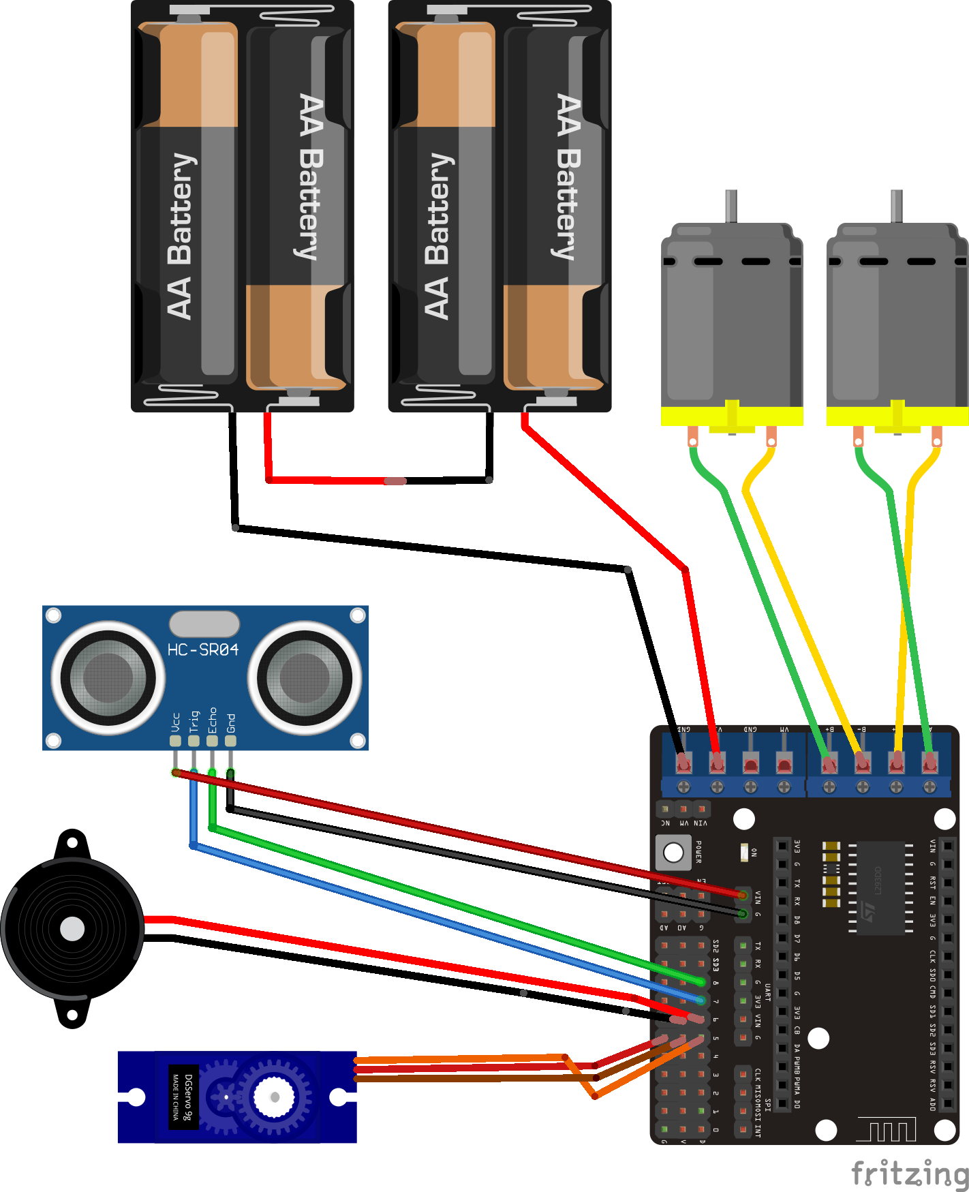
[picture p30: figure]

S e i t e 26 | 26

SCHALTPLAN
Bitte auch die Beschriftung auf den Platinen beachten! Diese können unterschiedlich sein.

Für den Betrieb muss noch der Jumper von VIN auf VM gesteckt werden.

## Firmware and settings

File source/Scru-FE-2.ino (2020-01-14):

/*-------------------------------------------------------
 *                                .:+oyhdmNNMMMMNNmdhyo+:.                            
                         -+ydMMMMMMMMMMMMMMMMMMMMMMMMMMdy+-                       
                     .+hNMMMMMMMMMMMMMMMMMMMMMMMMMMMMMMMMMMNh+.                   
                  .omMMMMMMMMMMMMMMMMMMMMMMMMMMMMMMMMMMMMMMMMMMmo.                
                /dMMMMMMMMMMMMMMMMMMMMMMMMMMMMMMMMMMMMMMMMMMMMMMMMd/              
             `+NMMMMMMMMMMMMMMMMMMMMMMMMMMMMMMMMMMMMMMMMMMMMMMMMMMMMNo`           
            +NMMMMMMMMMMMMMMMMMMMMMMMMMMMMMMMMMMMMMMMMMMMMMMMMMMMMMMMMNo          
          :mMMmyydMMMMMMMMMMMMMMMMMMMMMMNddNMMMMMMMMMMMMMMMMMMMMMMMMMMMMm:        
         sMMM/    .NMMMMMMMMmo:-/hMMMMMy   `hMMMMMMMMMMh. .hMMMMMMo` -mMMMy`      
       .dMMMN      yMMMMMMN+      yMMMMs    yMMMMMMMMMMs   `NMMMMh    dMMMMm.     
      -NMMMMm      yMMMMMs`      `dMMMMMmhhNMMMMMMMMMMMN`   oMMMM.   /MMMMMMN-    
     -NMMMMMm      sMMMh.       /NMMMMNo:-:yMMMMMMMMMMMMo   `MMMh    dMMMMMMMN-   
    `NMMMMMMd      sMm:       -dMMMMMM/.    dMMMMNy+:.```    yMM:    .``.:+hMMN.  
    hMMMMMMMd      o+       .yMMMMMMMMMM.   oMMm/            :MM            `sMd  
   /MMMMMMMMd             `oNMMMMMMMMMMM:   /Md`   `+yhhy-   `Md    /shhy/    :M+ 
   mMMMMMMMMd            /mMMMMMMMMMMMMM/   :M:   -NMMMMMs   `My    MMMMMMd    hN`
  :MMMMMMMMMd          -dMMMMMMMMMMMMMMM/   :M:   /MMMMMMs   `Mh    NMMMMMm    hM/
  yMMMMMMMMMd         :NMMMMMMMMMMMMMMMM/   :My    hMMMMM-   /MN    sMMMMM/   `MMy
  dMMMMMMMMMd           -+hNMMMMMMMMMMMM/   /MM/    +ddy-   `mMM+    +dmy-    hMMm
  NMMMMMMMMMd               -odMMMMMMMMM:   /MMM+          .dMMMM+          .hMMMM
  NMMMMMMMMMd      .`          `:smMMMMMy` .dMMMMmo-`  `-/yMMMMMMMmo:.  `./yMMMMMM
  dMMMMMMMMMd      sMms:`          .+NMMMMMMMMMMMMMMMMMMMMMMMMMMMMMMMMMMMMMMMMMMMm
  yMMMMMMMMMm      sMMMMMdo:         /MNs//sMMMMNNMMMMMMMMMMMMNysmMMMMMMMMMMMMMMMy
  :MMMMMMMMMm      sMMMMMMMMMho-    .dM+    sMd`  +MMMMMMMMMMM`   hMMMMMMMMMMMMMM/
   mMMMMMMMMm      yMMMMMMMMMMMMMdhmMMMm:../mM/   :MMMMMMMMMMM/   -MMMMMMMMMMMMMN 
   /MMMMMMMMN`     dMMMMMMMMMMMMMMMMMMMMmdNMMM.   oMMMMMMMMMMMm    hMMMMMMMMMMMM+ 
    hMMMMMMMMm+:-/hMMMMMNs+sNMMMMh+odMs`   :MN    hMMMMMMMNdhhh.   :MMMMMMMMMMMd  
    `mMMMMMMMMMMMMMMMMMM:   +MMMm    hys    ym    dMMMMd+.          mMMMMMMMMMN.  
     -NMMMMMMMMMMMMMMMMm    hMMMM/   .MM-   +m    mMMN:     `..     sMMMMMMMMN-   
      -NMMMMMMMMMMMMMMMs    MMMMMd    mM:   /m    dMM.   .yNMMMN.   +MMMMMMMN-    
       .dMMMMMMMMMMMMMMo   .MMMMMN    hM/   /N    hMm    dMMMMMM-   +MMMMMMm.     
         sMMMMMMMMMMMMMs   `NMMMMm    dM/   /M`   oMN`   sMMMMMM`   sMMMMMy`      
          -mMMMMMMMMMMMN`   /NMMM/   `MM:   /M:   :MMo   `hMMMMo    mMMMm:          
            +NMMMMMMMMMMh`   `//.    hMM:   /Ms   `MMM/    -+/.    sMMN+          
             `+mMMMMMMMMMm/        -dMMM:   oMm    mMMMy.        -hMNo`           
                /hMMMMMMMMMNyo++oymMMMMMmo/sNMMh//yMMMMMMds+++oymMd/              
                  .odMMMMMMMMMMMMMMMMMMMMMMMMMMMMMMMMMMMMMMMMMMmo.                
                     .+yNMMMMMMMMMMMMMMMMMMMMMMMMMMMMMMMMMMNh+.                   
                         ./sdNMMMMMMMMMMMMMMMMMMMMMMMMNdy+-                       
                              .:+oyhdmNNNMMNNNmdhyo+:.         
 *
 *
 * Pinbelegung
 * Interne LED        (D0) GPIO 16
 * Motor A PWM        (D1) GPIO 05
 * Motor B PWM        (D2) GPIO 04
 * Motor A direction  (D3) GPIO 00
 * Motor B direction  (D4) GPIO 02
 * Servo              (D5) GPIO 14
 * Piezo              (D6) GPIO 12
 * HC-SR04 trigger    (D7) GPIO 13
 * HC-SR04 echo       (D8) GPIO 15
 * free               (SDD3) GPIO 10
 * 
 * Logik
 * and             &&
 * and_eq          &=
 * bitand          &
 * bitor           |
 * not             !
 * not_eq          !=
 * or              ||
 * or_eq           |=
 * xor             ^
 * xor_eq          ^=
 * 
 --------------------------------------------------------*/

#include <ESP8266WebServer.h>
#include <ESP8266WiFi.h>
#include <ESP8266mDNS.h>
#include <ESP8266WiFi.h>
#include <ESP8266WebServer.h>
#include <ESP8266HTTPUpdateServer.h>
#include <Servo.h>
#include "pitches.h"  // must include open source pitches.h found online in libraries folder

//Set Wifi ssid and password
const char* ssid = "wifi-car";
const char* password = "1234";
const char* host = "car";
const char joystick_html[] PROGMEM="<html>\n\t<head>\n\t\t<meta charset=\"utf-8\">\n\t\t<meta name=\"viewport\" content=\"width=device-width, user-scalable=no, minimum-scale=1.0, maximum-scale=1.0\">\t\t\n\t\t<style>\n\t\tbody {\n\t\t\toverflow\t: hidden;\n\t\t\tpadding\t\t: 0;\n\t\t\tmargin\t\t: 0;\n\t\t\tbackground-color: #BBB;\n\t\t}\n\t\t#info {\n\t\t\tposition\t: absolute;\n\t\t\ttop\t\t: 0px;\n\t\t\twidth\t\t: 100%;\n\t\t\tpadding\t\t: 5px;\n\t\t\ttext-align\t: center;\n\t\t}\n\t\t#info a {\n\t\t\tcolor\t\t: #66F;\n\t\t\ttext-decoration\t: none;\n\t\t}\n\t\t#info a:hover {\n\t\t\ttext-decoration\t: underline;\n\t\t}\n\t\t#container {\n\t\t\twidth\t\t: 100%;\n\t\t\theight\t\t: 100%;\n\t\t\toverflow\t: hidden;\n\t\t\tpadding\t\t: 0;\n\t\t\tmargin\t\t: 0;\n\t\t\t-webkit-user-select\t: none;\n\t\t\t-moz-user-select\t: none;\n\t\t}\n\t\t</style>\n\n\t</head>\n\t<body>\n\n\t\n\t\t<div id=\"container\"></div>\n\t\t<div id=\"info\">\n\t\t\tBildschirm ber&uuml;hren und bewegen\n\t\t\t<br><b><button onclick=\"window.location.href = '/funktion1.html'\">Automatik AN / AUS</button>\n\t\t\t<p><b><button onclick=\"window.location.href = '/funktion2.html'\">Funktion 2</button>\n\t\t\t<br>\n\t\t\t</b><br/>\n\t\t\t<span id=\"result\"></span>\n\t\t</div> \n\t\t<script src=\"./virtualjoystick.js\"></script>\n\t\t<script>\n\t\t\tconsole.log(\"touchscreen is\", VirtualJoystick.touchScreenAvailable() ? \"available\" : \"not available\");\n\t\n\t\t\tvar joystick\t= new VirtualJoystick({\n\t\t\t\tcontainer\t: document.getElementById('container'),\n\t\t\t\tmouseSupport\t: true,\n\t\t\t\tlimitStickTravel\t: true,\n\t\t\t});\n\t\t\tjoystick.addEventListener('touchStart', function(){\n\t\t\t\tconsole.log('down')\n\t\t\t})\n\t\t\tjoystick.addEventListener('touchEnd', function(){\n\t\t\t\tconsole.log('up')\n\t\t\t})\n\t\t\tvar prevX = 0;\n\t\t\tvar prevY = 0;\n\t\t\tvar newX = 0;\n\t\t\tvar newY = 0;\n\t\t\tsetInterval(function(){\n\t\t\t\tvar outputEl\t= document.getElementById('result');\n\t\t\t\tnewX = Math.round(joystick.deltaX());\n\t\t\t\tnewY = Math.round(joystick.deltaY()) * -1;\n\t\t\t\toutputEl.innerHTML\t= '<b>Position:</b> '\n\t\t\t\t\t+ ' X:'+newX\n\t\t\t\t\t+ ' Y:'+newY;\n\t\t\t\tif ( newX != prevX || newY != prevY || newX!=0 || newY!=0){\n\t\t\t\t\tvar xhr = new XMLHttpRequest();\n\t\t\t\t\txhr.open('PUT', \"./jsData.html?x=\"+newX+\"&y=\"+newY)\n\t\t\t\t\txhr.send();\n\t\t\t\t\tsetTimeout(function(){xhr.abort();},100);\n\t\t\t\t}\n\t\t\t\tprevX = newX;\n\t\t\t\tprevY = newY;\n\t\t\t}, 150);\n\t\t</script>\n\t</body>\n</html>";
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
void loop()
{  
  /*--------------------------------------------------------------  
  * remove delay (one second)
  --------------------------------------------------------------*/
  currentMillis = millis();  //get the current "time" (actually the number of milliseconds since the program started)
  if (currentMillis - startMillis >= periode)  //test whether the period has elapsed
  { 
  startMillis = currentMillis;
  count_messung++;
  count_wait++;
  }

  // Prüfen, ob jemand per WLAN zugreift
  client_connected = WiFi.softAPgetStationNum(); 

  if (automatik_helper == false && client_connected < 1) {
    if (count_wait >= 254) {
      automatik = true;
      automatik_helper = true;
    }
  }

  /*-----------------------------------------------------------------
  * Distanz Messung
  ----------------------------------------------------------------*/
  if ( count_messung > 1 ) {
    distance = distMes();         // Messe die Distanz mit dem Ultraschallmodul. Ergebnis in der Variablen in cm 
  if ( automatik == 1 ) {
    digitalWrite(espLED, !digitalRead(espLED));
  }
  }

// Handle Client
    server.handleClient();
        
// Autonomes fahren aktivieren, wenn Scru-FE eingeschaltet und kein Client verbunden ist.
    
  if (automatik == true) {

  // Reagiere auf die gemessene Entfernung  
    if (distance >= MIN_DIST)    // Wenn die Entfernung größer, gleich Mindestenfernung ist, dann...
    {
      //Serial.println(F("motorForward"));
      motorForward();          // Motor vorwärts
    }
    else
    {
      //Serial.println(F("motorHalt"));
      motorStop();
      sound();                    // Ton ausgeben
      motorBack(500);
      headRight();                // Servo nach rechts drehen
      distance = distMes();       // Messe die Distanz mit dem Ultraschallmodul. Ergebnis in der Variablen in cm

      if (distance >= MIN_DIST) // Wenn die Entfernung größer, gleich Mindestenfernung ist oder die Entfernung kleiner, gleich Null, dann...
    {
      //Serial.println(F("motorRight"));
      motorRight(400);             // Rechts drehen
      headCenter();                 //Drehe den Servo in die Mitte
    }
    else
    {
      headLeft();               // Servo nach links drehen
      distance = distMes();       // Messe die Distanz mit dem Ultraschallmodul. Ergebnis in der Variablen in cm

      if (distance >= MIN_DIST) // Wenn die Entfernung größer, gleich Mindestenfernung ist oder die Entfernung kleiner, gleich Null, dann...
    {
      motorLeft(400);              // Links drehen
      //Serial.println(F("motorLeft"));
      motorBack(500);           // Rückwärts fahren für Zeit in ms 
      headCenter();                 //Drehe den Servo in die Mitte
    }
    else
    {
      motorBack(500);           // Rückwärts fahren für Zeit in ms 
      headCenter();                 //Drehe den Servo in die Mitte
    }
  }
 }
}

}

/*--------------------------------------------------------------------
 * Ab hier werden Unterprogramme erstellt
 *--------------------------------------------------------------------*/
void headRight(void)
{ 
  myservo.write(0);      // Servo auf 80 Grad Drehwinkel setzen
  delay(500);             // 500ms warten
}

void headLeft(void)
{
  myservo.write(180);     // Servo auf 220 Grad Drehwinkel setzen
  delay(500);             // 500ms warten
}

void headCenter(void)     
{
  myservo.write(90);     // Servo auf 130 Grad Drehwinkel setzen
  delay(500);             // 500ms warten
}
 
 void motorStop(void)
{
  //MotorA
  digitalWrite(AIN1, 0);
  analogWrite(PWMA, 0);
  //MotorB
  digitalWrite(BIN1, 0);
  analogWrite(PWMB, 0);
}

void motorForward()
{
 //Move Forward
 //MotorA
  digitalWrite(AIN1, 0);
  analogWrite(PWMA, 1000);
  //MotorB
  digitalWrite(BIN1, 0);
  analogWrite(PWMB, 1000);
  }
  
void motorBack(unsigned long delaytime)
{
  //Move Backward
 //MotorA
  digitalWrite(AIN1, 1);
  analogWrite(PWMA, 800);
  //MotorB
  digitalWrite(BIN1, 1);
  analogWrite(PWMB, 800);
  delay(delaytime);
  motorStop();
}

void motorLeft(unsigned long delaytime)

{
  //Motors Turn Left
  //MotorA
  digitalWrite(AIN1, 1);
  analogWrite(PWMA, 1000);
  //MotorB
  digitalWrite(BIN1, 1);
  analogWrite(PWMB, 0);
  delay(delaytime);
  motorStop();
}

void motorRight(unsigned long delaytime)

{
  //Motors Turn Right
 //MotorA
  digitalWrite(AIN1, 1);
  analogWrite(PWMA, 0);
  //MotorB
  digitalWrite(BIN1, 1);
  analogWrite(PWMB, 1000);
  delay(delaytime);
  motorStop();
}
 
 int distMes(void)
{
  // Ping Utrasonic Sensor to find obstacles within distance in cm
  int duration;
  // Sets the trigPin on HIGH state for 10 micro seconds
  digitalWrite(trigPin, LOW);
  delayMicroseconds(5);
  digitalWrite(trigPin, HIGH);
  delayMicroseconds(10);
  digitalWrite(trigPin, LOW);

  // Reads the echoPin, returns the sound wave travel time in microseconds
  duration = pulseIn(echoPin, HIGH);

  // Calculating the distance
  distance= (duration / 2) / 29.1;

  // Prints the distance on the Serial Monitor
  Serial.print("Distance: ");
  Serial.println(distance);
  count_messung = 0;
  return distance;
}

void handleVirtualJoystickJS(){
  server.send_P(200,"application/javascript",virtualjoystick_js);
}

void handleJoystickHtml()
{
 server.send_P(200,"text/html",joystick_html); 
}

//This function takes the parameters passed in the URL(the x and y coordinates of the joystick)
//and sets the motor speed based on those parameters. 
boolean Direction;

void handleFunktion1() {
   if (automatik == true) {
    automatik = false;
    digitalWrite(espLED, HIGH);
   } else if (automatik == false) {
    automatik = true;
   }
   
  server.send_P(200,"text/html",joystick_html);
  Serial.println("Funktion1 aufgerufen ...");
  Serial.print("Automatik: ");
  Serial.println(automatik); 
}

void handleFunktion2() {
  server.send_P(200,"text/html",joystick_html); 
  Serial.println("Funktion2 aufgerufen ...");
  MarioSound();
}

void handleJSData(){

  int x = server.arg(0).toInt() * 10;
  int y = server.arg(1).toInt() * 10;
  
  Serial.print("x=");
  Serial.println(x);
  Serial.print("y=");
  Serial.println(y);

 if (( x < 0 ) && (y > 0)) {
  aSpeed = y;
  bSpeed = x*(-1) + y; 
 }
 if (( x > 0 ) && (y > 0)) {
  aSpeed = y + x;
  bSpeed = y;
 }
 if (( x < 0 ) && ( y < 0 )) {
  aSpeed = y*(-1);
  bSpeed = y*(-1) + x*(-1);  
 }
 if (( x > 0 ) && (y < 0)) {
  aSpeed = y*(-1) + x;
  bSpeed = y*(-1);
 }
 if (( x == 0) && ( y == 0 )) {
  aSpeed = 0;
  bSpeed = 0;
 }
   
  //set the direction based on y being negative or positive
  if ( y >= 0){
    Direction = 0; 
  } else {
    Direction = 1; 
  }
  
  aSpeed = constrain(aSpeed , 0, 1023); // Den PWM Wert zwischen 0 und 1023 begrenzen
  bSpeed = constrain(bSpeed , 0, 1023); // Den PWM Wert zwischen 0 und 1023 begrenzen
    
  Serial.print("aSpeed=");
  Serial.println(aSpeed);
  Serial.print("bSpeed=");
  Serial.println(bSpeed);

  Serial.print("Direction Motor A=");
  Serial.println(Direction);
  Serial.print("Direction Motor B=");
  Serial.println(Direction);
    
//MotorA
  digitalWrite(AIN1, Direction);
  analogWrite(PWMA, aSpeed);
//MotorB
  digitalWrite(BIN1, Direction);
  analogWrite(PWMB, bSpeed);

  //return an HTTP 200
  server.send(200, "text/plain", "");   
}

void sound(void)
{
  //Melodie
  tone(Buzzer, 647);          //  E start of power up tone! 432HZ
  delay(150);
  tone(Buzzer, 770);          //  g
  delay(100);
  tone(Buzzer, 1295);          // High E
  delay(100);
  tone(Buzzer, 1027);          // c
  delay(100);
  tone(Buzzer, 1153);          // d
  delay(150);
  tone(Buzzer, 1539);          // High G
  delay(100);
  noTone(Buzzer);
}

void readySound(void)
{
  //sound
  tone(Buzzer, 1027); // c
  delay(200);
  tone(Buzzer, 647); // e
  delay(200);
  tone(Buzzer, 770); //  g
  delay(200);
  tone(Buzzer, 1027); // c
  delay(200);
  noTone(Buzzer);
}

void distSound(void)
{
  //sound
  tone(Buzzer, 1027); // c
  // input no delay 
  delay (100);
   noTone(Buzzer);
}

void MarioSound(void)
{
  // Play coin sound   tone(Buzzer,NOTE_B5,100);
  delay(100);
  tone(Buzzer,NOTE_E6,850);
  delay(800);
  noTone(Buzzer);
  
  delay(500);  // pause 2 seconds

  // Play 1-up sound
  tone(Buzzer,NOTE_E6,125);
  delay(130);
  tone(Buzzer,NOTE_G6,125);
  delay(130);
  tone(Buzzer,NOTE_E7,125);
  delay(130);
  tone(Buzzer,NOTE_C7,125);
  delay(130);
  tone(Buzzer,NOTE_D7,125);
  delay(130);
  tone(Buzzer,NOTE_G7,125);
  delay(125);
  noTone(Buzzer);

  delay(500);  // pause 1 seconds

  // Play Fireball sound
  tone(Buzzer,NOTE_G4,35);
  delay(35);
  tone(Buzzer,NOTE_G5,35);
  delay(35);
  tone(Buzzer,NOTE_G6,35);
  delay(35);
  noTone(Buzzer);
}
